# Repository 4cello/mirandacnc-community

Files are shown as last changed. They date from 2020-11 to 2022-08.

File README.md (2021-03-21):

# mirandacnc-community
This repository contains a collection of modifications and tips of the MirandaCNC, a CNC machine designed by [Ivan Miranda](https://www.youtube.com/user/superazote). The source files for the machine can be purchased in [Ivan Miranda's Shop](https://ivanmiranda.com/collections/all).

## Contents
### [BOM Modifications](bom_modifications.md)
Contains changes to the BOM to take into account before you start building.

### [Jigs](jigs)
Contains printable helpers, for example to align and center the linear rails.

### [Modifications](modifications)
Contains changed/improved versions of Ivan's STL files, as well as useful additional parts.

### [Printing Tips](printing_tips.md)
Contains slicer settings and ways to get your parts to print easier.

### [Assembly Tips](assembly_tips.md)
Contains tips to consider while assembling the machine, ranging from measuring to minor layout changes.

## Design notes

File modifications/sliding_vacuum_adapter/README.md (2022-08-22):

# Sliding vacuum adapter
Adds a vacuum connection that can slide up and down independently of the Z axis.
It mounts to the side of the carriage.

The design is heavily inspired by Ivan's smaller CNC machine, as seen in [this YouTube video](https://youtu.be/ctyLjOHg7Ag?t=791).

This is not finished, and I probably won't continue to design this, because I attached my Y axis motors to the inside of the sideplates to save footprint, but this first design iteration collides with the motors.

I tried a test cut, but only mounted this part with double sided tape, which introduced a little to much flex, but worked in principle.
([Video of test cut](https://gfycat.com/clutteredfancygallowaycow))

*Creator: @4cello#7203*

## Part descriptions
### cnc_vacuum_mount
The upper part of the system. It attaches to the carriage via 2 M5 bolts. It accepts a vacuum hose with a 36mm endpiece.
### sliding_succ
The sliding part of the system. It goes into the bottom of the `cnc_vacuum_mount` and is clamped at the desired height using a M5 bolt.
### vac_bracket
The bracket that clamps down on the vacuum hose end piece. Mounted and clamped using M5 bolts.

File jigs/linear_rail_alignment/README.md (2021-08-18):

# Linear Rail Alignment Jig
This part helps to align the linear rails in the center of the aluminium profiles. This makes it easier to mark and drill the holes without worrying that the rail has moved.

*Creator: @Hytech#2100*

## Part descriptons
### rail_alignment_jig_30mm
The jig for the metric profiles. (30mm)

### rail_alignment_jig_1.25inch
The jig for imperial profiles. (1 1/4in)

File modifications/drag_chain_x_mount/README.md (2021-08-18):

# Drag Chain X Mount
In the original design, the X axis drag chain reaches far outside of the frame, which takes up a lot of additional space. To prevent this, the drag chain can instead be positioned along the rear bridge profile as seen below.
Drag chain

*Creator: @Hytech#2100*

## Part descriptions
### Drag_Chain_Upper_X-Mount_40mm
Attaches to the Z motor mount as seen in the image above. Holes need to be drilled into the motor mount.

### Drag_Chain_Lower_X-Mount_40mm

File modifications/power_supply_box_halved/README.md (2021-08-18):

# Power Supply Box (Halved)
Due to its prodigious size (30cm long), the provided power supply box can be challenging to fit on a printer's bed.
To make it easier to print, the box was split in halves, which should fit on most printers.

The parts are mostly symmetrical so they can exchanged easily. For a full box, you need a combination of the following:
 - 2x PSBOX_HALF
 - 2x PSBOX_HALF_CABLE_HOLE
 - 1x PSBOX_COVER_CUTOUTS
 - 3x any combination of PSBOX_COVER_BLANK and PSBOX_COVER_LOGO
 
The halves of the box itself can be connected with M3x22 screws, which are already on the BOM, since you probably bought spares.
M3 nuts can be used to further tighten the assembly. The shape of the cut should make it easier to align the halves.

The covers snap together with a dovetail, but if you find the connection to be to flimsy, you could connect them with glue, 
filament welding (with a soldering iron or 3D pen) or simply with adhesive tape on the inside.

The mounting holes are compatible with the original power supply box.

*Creator: @4cello#7203*
## Part descriptions
### PSBOX_HALF
A half of the power supply box. Two of these can be connected with M3x22mm screws and nuts. 

### PSBOX_HALF_CABLE_HOLE
The same as PSBOX_HALF, but with a half circle cutout in the short wall for the output cables of the power supply.

### PSBOX_COVER_BLANK
A half of the cover for the box. Two of these can be connected with their dovetails. This version is just a blank cover, much like the back cover of the original. Compatible with all other cover variants.

### PSBOX_COVER_CUTOUTS
A modified version of PSBOX_COVER_BLANK with the cutouts for emergency stop button and power socket + switch. Compatible with all other cover variants.

### PSBOX_COVER_LOGO
A modified version of PSBOX_COVER_BLANK with the lightbulb logo from Ivan Miranda's website embossed into it. Compatible with all other cover variants.

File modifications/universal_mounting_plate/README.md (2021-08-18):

# Universal mounting plate
This part is my base solution to mount different things to the vertical slider. It is mounted in place of the router bracket and contains several mounting solutions.

There is a 3x3 grid of holes, where an M5 hex nut can be pressed into (and glued in place if necessary). The grid spacing is 25mm.

Left and right of the grid's center column are two slots which hold M5 nuts that can slide up and down. The slots are 25mm apart and allow for more flexible but less repeatable attaching of parts. The slots can be plugged by gluing the slot plug on top, or simply with hotglue.

The slots have an included sacrificial layer to allow the plate to be printed face-down. After printing, simply remove the bridging layer from the slot. If some debris remains, inserting a nut and sliding it around a few times inside the slot should clean it up.

*Creator: @4cello#7203*

## Part descriptions
### universal_plate
The mounting plate itself as described above.
### universal_plate_slot_plug
A simple part that can plug the holes of the slots to prevent nuts falling out. Optional, as the same can be accomplished with hotglue.

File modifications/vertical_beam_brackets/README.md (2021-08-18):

# Vertical Beam Brackets
These parts help to align the vertical beams with the horizontal frame. Also, they look pretty cool.
The vertical beams still make contact with the frame, so you can still apply the full clamping force by tightening the threaded rods without the brackets breaking.

*Creator: @Hytech#2100*
## Part descriptions
### Frame_Lower_Side_Bracket
A bracket for the lower side of the vertical beam.

### Frame_Upper_Side_Bracket
A bracket for the upper side of the vertical beam. Modified version of the lower bracket to stay clear of the linear rails mounted to the upper frame.

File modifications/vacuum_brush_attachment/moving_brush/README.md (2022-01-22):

# Moving brush attachment for the vacuum funnel

*Creator: @4cello#7203*

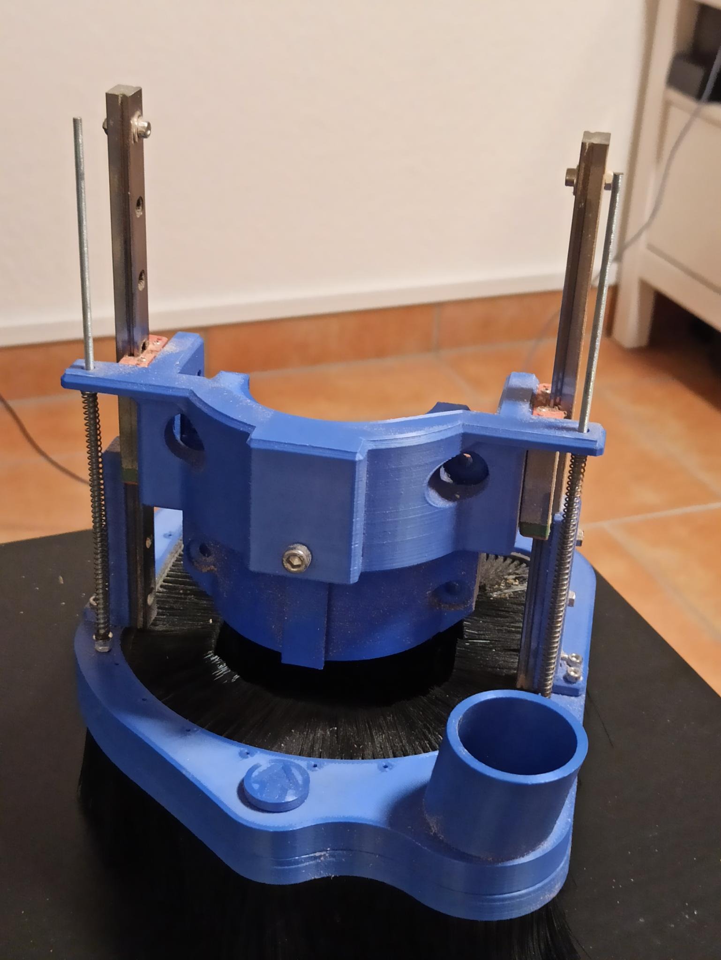
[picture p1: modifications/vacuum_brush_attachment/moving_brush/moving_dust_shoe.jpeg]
Moving Dust Shoe Image


## Part descriptions

This is a pretty poor attempt to create a dust shoe that moves up and down independently from the router
(or at least: more independent). It attaches to the vertical slider using the 200mm rails I had left over after
upgrading my Z travel with 250mm rails. To push the dust shoe against the wasteboard/workpiece, springs are installed between
router clamp and dust shoe. However, it is very hard to get the length and stiffness of the springs tuned just right so the
bristles of the brush don't get squished.

The dust shoe itself is designed to use "Mink Flex FBL3002" brush strips, I used a bristle length of 50mm. The slot for the brush strip
is 6mm wide and 7mm deep. The same brush strip is also used to provide a seal against the router (+clamp) even when it moves up or down.

The brush part itself is magnetically attached to the rest of the mechanism so it can be removed for tool changes
(although it can be annoying to get it past the endmill...).

The dust shoe has 2 holes: 1 for the vacuum hose and 1 for pressurized air. I don't actually know how practical this is going to be, but I thought it could be helpful to blow onto the cutting bit to send heavier particles airborne for the shop vac to suck up.

## Future work
While this version improves on the shortcomings of the fixed brush attachment, it is fundamentally flawed: Since the height of the
workpiece is usually constant during a job, the dustshoe doesn't actually need to apply varying pressure depending on the cutting
depth. Instead, it would be much more reasonable if the rails were attached to the carriage, so the height could be adjusted once
for each job.

Alexandre Chappel made a dust shoe based on this principle in this YouTube video: https://www.youtube.com/watch?v=qFIYdQG0TTE

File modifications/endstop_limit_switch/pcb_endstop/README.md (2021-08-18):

# Rail endstop with limit switch mount
When building the geared version with HTD belts, this part can be used instead of the default endstops.

The part can hold PCB mounted limit switches, like [these](https://www.ebay.com/itm/10X-Mechanical-End-Stop-Endstop-Limit-Switch-CNC-3D-Printer-RAMPS-1-4-Arduino-/363454474395) or [these](https://www.aliexpress.com/item/32789789727.html).

Currently, the endstop can't be used with the GT2 version of the CNC machine because it has no belt mounting attachment. 
If anybody gets around to add the teeth, please share your files!

*Creator: @Hytech#2100*

## Part descriptions
### Endstop_with_switch_X_LH
Endstop for the left-hand side of the X axis.
### Endstop_with_switch_X_RH
Endstop for the right-hand side of the X axis.
### Endstop_with_switch_Y_Fr
Endstop for the front side of the Y axis.
### Endstop_with_switch_Y_Rr
Endstop for the rear side of the Y axis.
### Z_Limit_Switch_Mount_Both
Endstop for the Z axis. The part is mounted directly to the carriage in the corresponding orientation, depending on if you want a Z+ or Z- endstop or both. The limit switch is activated by the included lever.
### Z_Limit_Switch_lever
The lever which activates the Z limit switch(es). Mount this to the vertical slider at such a position that it hits the Z limit switch at the right height.

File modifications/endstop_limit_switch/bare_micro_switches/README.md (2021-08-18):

# Rail endstop with limit switch mount
When building the geared version with HTD belts, this part can be used instead of the default endstops.

The part features a mounting slot to hold widely available 20x10x6mm microswitches. 
M2.5 nuts can be inserted into openings and pushed into the slots to firmly secure the switch in place.
I used M2.5x14mm screws, since they fit through the holes in my microswitches and are short enough to not poke out of the backside.

The endstop is mounted directly to the aluminium profile like the original part, but the location of the mounting holes is different.

Currently, the endstop can't be used with the GT2 version of the CNC machine because it has no belt mounting attachment. 
If anybody gets around to add the teeth, please share your files!

*Creator: @4cello#7203*
## Part descriptions
### ENDSTOP_LIMIT_SWITCH
The modified rail endstop as descriped above.

### z_limit_trigger
A small arm that can be screwed into drilled holes on the vertical slider. Can be used to trigger limit switches which are screwed to the carriage.

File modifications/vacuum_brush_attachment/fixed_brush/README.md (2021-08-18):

# Brush attachment for the vacuum funnel
These parts allow for attaching a brush to the vacuum funnel to catch as much of the dust as possible.

The brush holder is attached to the vacuum funnel with 4 M3 screws with at least 20mm length (better ~30mm) to allow for removing the brush if it isn't required.

This design is not great and should probably not be used for various reasons:
- The brush extends a fixed distance down, which means the bristles get squished, especially when using a short cutting tool. This introduces a lot of friction, as well as bending the bristles so they don't catch as much dust.
- The brush has to be removed for a toolchange, which can be quite tedious.
- The brush strip I designed this for was very annoying to work with, both in terms of bending it into the desired shape and glueing it into the printed part.

I attempted to address this issues with the [moving brush design](../moving_brush), which uses 200mm MGN12H rails to slide the dust shoe up and down.

*Creator: @4cello#7203*

## Part descriptions
### VACUUM_FUNNEL_CUSTOM
A slight modification of the default VACUUM FUNNEL part. 4 holes were added around the bottom to mount the brush holder to. You might want to close these holes with bolts (or hot glue) if you want to use it without the brush (for maximum vaccum power!).

### VACUUM_FUNNEL_BRUSH_HOLDER
The part which holds the brush. It has a slot which is 6mm wide and 10mm deep and can hold the common brush strips, which are 5mm wide. The brush strip should be glued into the slot, since it is an intentionally loose fit.
After the glue has hardened, you will want to drill through the mounting holes into the fabric part of the strip to open up a path for the screws.

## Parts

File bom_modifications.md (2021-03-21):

# Universal BOM Modifications
## Z-Travel
### Vertical Beams
When using 60mm vertical beams, the Z travel is quite limited, 
to the extent that it can be challenging to change cutting bits even when moving the slider all the way to the top.

To combat this, you can use longer vertical beams. While some have doubled the length, going from 60mm to 90-100mm seems more reasonable
to ensure that the cutting bit can reach all the way down to the wasteboard, as well as giving a little peace of mind when considering rigidity of the frame.

When extending the vertical beams, you need to consider the following:
- The threaded rods that run through the vertical beams need to be extended by the same amount
- The stock electronics and power supply boxes don't fit between the upper and lower frame, so you will need modified versions. Before designing your own, try checking the [modifications](modifications) folder or ask around on the Discord, chances are that somebody has already done the work.

### Z Rails
While extending the vertical beams gives you more travel in the upward Z direction, there is also something to be gained in the downward direction.

The stock 200mm linear rails used to attach the vertical slider to the carriage are a little to short, so the blocks slip (at least partially) off the rails before the theoretical minimum Z position is reached.

A simple fix is to use 250mm linear rails and mount them in such a way that they are still flush with the bottom of the slider, but stick out over the top. While this doesn't look as clean, it ensures that your machine can utilize the full Z travel as constrained by the slider and carriage parts.

# Reduction Version (HTD-5M)
## Screw Lengths
The stepper motor screws are listed as M3x50mm in the BOM, which is insanely long. While it is not unthinkable, that you need 50mm screws for your motors, you probably want to use M3x16 or M3x18mm ones.

## Bearings
When using 608 bearings for belt redirection, it is possible that the clearance between the "upwards" and "downwards" part of the belt is to tight. Instead, use 698zz bearings, which have a smaller outside diameter. You will need to add some washers between the sideplate and the bearings, because the bearings are also thinner.
# Base Version (GT2)
nothing here yet

# Full Metal Version
nothing here yet

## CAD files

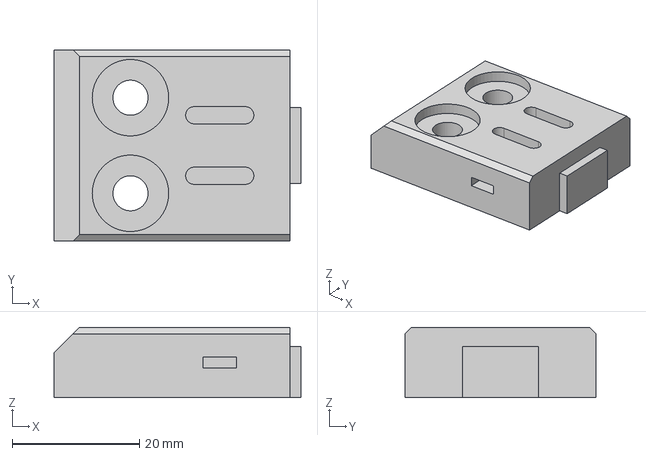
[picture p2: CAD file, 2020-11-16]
modifications/endstop_limit_switch/bare_micro_switches/endstop_limit_switch.step
38.8 x 30.0 x 11.0 mm

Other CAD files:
jigs/linear_rail_alignment/rail_alignment_jig_1.25_inch.stl
modifications/drag_chain_x_mount/Drag_Chain_Upper_X-Mount_40mm.stl
modifications/duet_box/duet_box_lid.stl
modifications/endstop_limit_switch/bare_micro_switches/z_limit_trigger.stl
modifications/endstop_limit_switch/pcb_endstop/Z_Limit_Switch_lever.stl
modifications/power_supply_box_halved/100mm/PSBOX_100_COVER_CUTOUTS.stl
modifications/power_supply_box_halved/PSBOX_COVER_BLANK.stl
modifications/sliding_vacuum_adapter/alternate_vac_mount_supported.stl
modifications/universal_mounting_plate/universal_plate.stl
modifications/vacuum_brush_attachment/fixed_brush/VACUUM_FUNNEL_CUSTOM.stl
modifications/vertical_beam_brackets/Frame_Upper_Side_Bracket.stl
jigs/linear_rail_alignment/rail_alignment_jig_30mm.stl
modifications/drag_chain_x_mount/Drag_Chain_Lower_X-Mount_40mm.stl
modifications/duet_box/duet_box.stl
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

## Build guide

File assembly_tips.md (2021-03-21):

# Universal Assembly Tips
Remember to check out the [jigs](jigs) folder for useful assembly helpers.

## X Axis Installation
1. Use calipers depth gauge to center the first rail and get the correct offset from 
the side, the important thing here is the distance from the edge. How in the middle it is 
and how far it is from the side is not as important as making sure the distance to the 
edge is equal. (Or just use the [rail alignment jig](jigs/linear_rail_alignment))
2. Clamp it down, recheck square, and punch two holes on the end with a transfer
punch. Alternatively, you could use a normal punch and try to align it, or a drill bit. All 
you need is a mark. Then take the rail off, use a normal punch to define that hole, and drill and tapp. 
3. Repeat step 2 for all 22 other holes but instead of clamps, I used the bolts on the 
rail. Use fluid while drilling and while tapping. 
4. That is the first rail done. For the 2nd do the same thing exept instead of trying to 
center the rail copy the offset from the first rail. If you do this make sure that you are 
measuring from the bottom or top of each rail. You need them to have the same offset or 
as close as possible. 
5. Install the screws into the rail and the beam onto the frame. 
6. Install the carriage onto the x, use m3x20 here. Some holes may need to be drilled larger to fit.  

## Rail alignment
"the Y-axis rails aren't that important, but in the X both rails need to be parallel 
so don't fasten the rails until the carriage is installed, then move the carriage to one side, fasten 
a couple of bolts on that side, slide it to the other side and fasten a couple of bolts on the other 
side and then you can go and fasten everything" -Ivan

## X Axis Drag Chain
The X axis drag chain sticks out really far, which pretty much doubles the footprint the machine requires. Instead, the drag chain can be installed along the back beam of the X axis, so it is fully confined to the machine frame.

Check out [this modification](modifications/drag_chain_x_mount) for an image and STL files to help with this.

# Reduction Version (HTD-5M)
## Belt Tensioners
### X axis
- Install tensioner on left side (away from carriage motor), so the belt bearings don't crash into it. You will need to drill a hole into your printed part for the screw to fit through.
- Doesn't require an extra belt tensioner, since screw goes through left carriage instead. However, you might want to print the mirrored version of the belt tensioner, if you stick with the stock ones (although I'm not sure if this makes a functional difference).

### Y axis
- Move tensioners as far back as possible, to prevent x axis crashing into it.

## Endstops
- Use GT2 belt clip thingys as endstops only, no belts attached.
- There are custom endstops available [here](modifications/endstop_limit_switch), where limit switches can be attached to. However, these are untested

# Base Version (GT2)

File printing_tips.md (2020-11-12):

# Printing Tips
Some of the parts are very large and/or challenging to print. This is a collection of tips to help with printing the parts for the MirandaCNC.

## General Slicer Settings
### Perimeters
The number of perimeters is the most important factor for stability. 

Ivan recommends 3 perimeters and 3 top/bottom shells, but feel free to slap on 1-2 more, just for good measure.

### Infill
While higher infill also improves stability, it also increases the mass of the part, which dampens vibrations.

Ivan used 30% infill for his parts. Most slicers will give you an estimate of filament consumption of a part, so keep an eye on that.

## Specific Components

### Power Supply Box
The original power supply box is 30cm long, which doesn't fit on many printers. This repository contains a version, where the box itself and the covers are cut in half to a more manageable size. The STL files can be found [here](modifications/power_supply_box_halved). The parts are designed to be redundant, so a full box consists of the following parts:

 - 2x PSBOX_HALF
 - 2x PSBOX_HALF_CABLE_HOLE
 - 1x PSBOX_COVER_CUTOUTS
 - 3x any combination of PSBOX_COVER_BLANK and PSBOX_COVER_LOGO

### Carriage
The carriage is another very large part, however there are multiple ways to handle it.

The bottom of the part is not critical, so you can just cut it off. Just make sure you don't cut off any mounting holes for the sliding blocks. Also, double check that you cut off the bottom, not the top. [Image](https://i.imgur.com/QEvIyVc.png)

If the part won't fit flat on the bed, you can print it standing up.
You can add [sacrificial layers](https://i.imgur.com/FXWv8qv.png) ([Explanation video](https://www.youtube.com/watch?v=upqTE8EPZIQ)) to cut down on plastic waste and printing time by removing the need for supports. 
Adding layers in the red spots in the image allows the 3D printer to simply use bridging. 
The sacrificial layers can be easily removed after the print using a knife. 
Sacrificial layers can be created either in the CAD program of your choice or directly in some slicers (like PrusaSlicer). 
Just make sure that the thickness matches your layer height to ensure that your slicer generates exactly one layer.

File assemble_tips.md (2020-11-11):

# MirandaCNC Assembly Tips
## Belt Tensioners
X axis:
- Install tensioner on left side (away from carriage motor), so the belt bearings don't crash into it.
- Doesn't require an extra belt tensioner, since screw goes through left carriage instead.

Y axis:
- Move tensioners as far back as possible, to prevent x axis crashing into it.

## Endstops
- Use GT2 belt clip thingys as endstops only, no belts attached.
- There are custom endstops available, where limit switches can be attached to. 
    However, this version doesn't have a belt clip (yet?), so it is only suitable for the HTD 5M version.

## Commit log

2020-11-11 clarified that assembly instructions are for HTD5M
2020-11-16 Added endstop sources
    [endstop_limit_switch.f3d, endstop_limit_switch.step]
2020-11-16 Added power_supply_box_halved sources
    [power_supply_box_halved.f3d, power_supply_box_halved.step]
2020-11-16 Added vacuum funnel with brush attachment. Improved some modification READMEs.
    [VACUUM_FUNNEL_BRUSH_HOLDER.stl, VACUUM_FUNNEL_CUSTOM.stl]
2020-11-16 Added vacuum brush sources.
    [vacuum_brush_attachment.f3d, vacuum_brush_attachment.step]
2021-02-13 Added some new parts and updated descriptions
    [Drag_Chain_Lower_X-Mount_40mm.stl, Drage_Chain_Upper_X-Mount_40mm.stl, Frame_Lower_Side_Bracket.stl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]
2021-03-21 Restructured assembly instructions, added BOM modifications
2021-03-21 Added better X drag chain mounting instructions
2021-08-18 Added credit for the modifications and moved some designs into subfolders to prepare for alternate versions
    [ENDSTOP_LIMIT_SWITCH.stl, VACUUM_FUNNEL_BRUSH_HOLDER.stl, VACUUM_FUNNEL_CUSTOM.stl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]
2021-08-18 Added Hytech's limit switch designs
    [Drag_Chain_Upper_X-Mount_40mm.stl, Endstop_Y_LH_Both.stl, Endstop_with_switch_X_LH.stl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]
2021-09-11 added duet box
    [duet_box.stl, duet_box_lid.stl]
2022-01-27 Added 100mm version of the PS box
    [PSBOX_100_COVER_BLANKstl.stl, PSBOX_100_COVER_CUTOUTS.stl, PSBOX_100_COVER_LOGOstl.stl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]
2022-08-16 Added sliding vacuum adapter, added git lfs
    [Drag_Chain_Lower_X-Mount_40mm.stl, Drag_Chain_Upper_X-Mount_40mm.stl, ENDSTOP_LIMIT_SWITCH.stl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]
2022-08-19 Added alternate sliding vacuum version
    [Sliding_Vacuum_Adapter_v3.f3z, Sliding_Vacuum_Adapter_v5.f3z, alternate_sliding_succ.stl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]
2022-08-19 Added more clearance for the M8 nut
    [Sliding_Vacuum_Adapter.f3z, alternate_vac_mount.stl]
2022-08-19 Updated F3Z with added clearance
    [Sliding_Vacuum_Adapter.f3z]
2022-08-22 Added version for alternate vacuum mount with supports
    [alternate_vac_mount_supported.stl]
